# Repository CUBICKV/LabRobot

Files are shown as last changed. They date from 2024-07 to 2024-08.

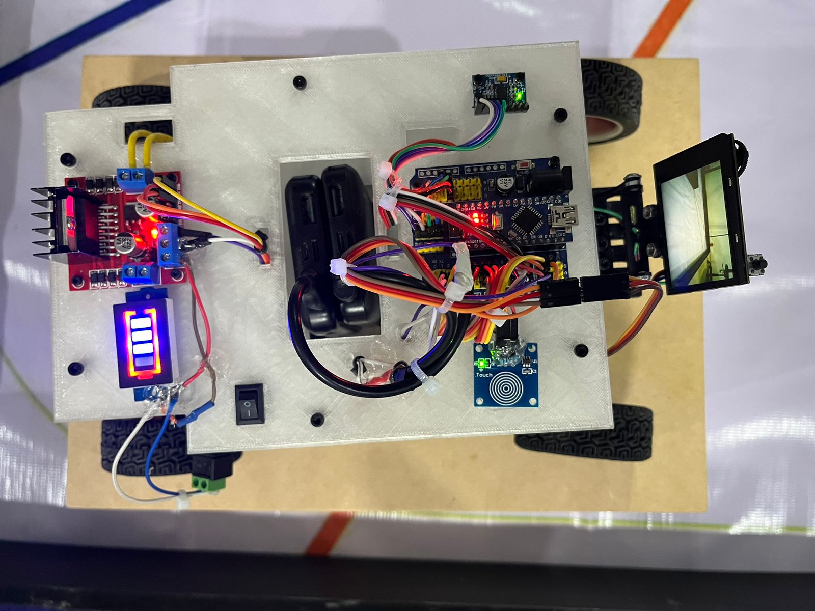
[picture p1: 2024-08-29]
v-photos/SUPERIOR.jpg

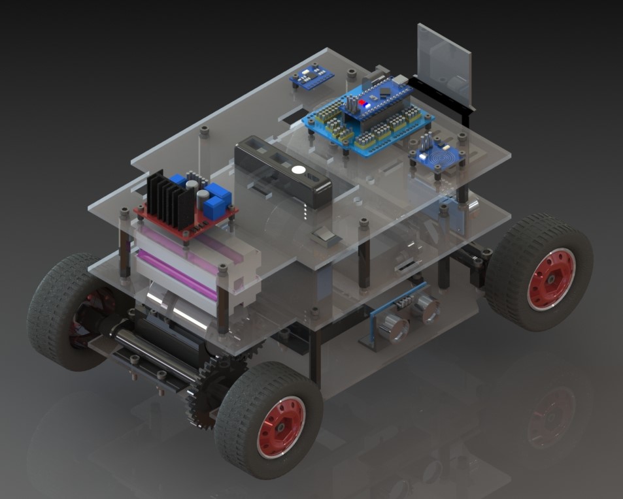
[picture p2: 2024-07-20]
v-photos/ISOMETRICO_4.JPG

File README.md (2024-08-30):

LabRobot
====

El robot nombrado “MATE” es un vehículo autónomo diseñado en un software de CAD, y con circuitos en simuladores electrónicos, programado en la plataforma ARDUINO.
Para el sistema de control, se utilizó una placa de expansión de Arduino nano la cual nos permitió usar sus pines junto a los cables jumpers, para ahorrar nodos de soldadura en el cableado.
Los niveles lógicos a trabajar para el control, se establecieron a 5v, el voltaje de funcionamiento del Arduino nano. Los modulos seleccionados fueron los que tuvieron ese mismo nivel.
Los componentes junto con sus funciones son:
Giroscopio MPU6050: Es un módulo que me permite saber la orientación y ángulo de giro en el Eje Z, para poder conocer mi sentido de giro y mi localización angular en el plano.
Sensor Touch de inducción: Es un sensor táctil, que realiza la misma función de un botón, pero le da una mayor estética al encendido, y nos ahorra el cableado del botón, al igual que es más grande que un botón convencional y menos estorboso
Micro Switch: Nos envía la energía de la Power bank para poder alimentar el sistema de control electrónico.
Puente H: Este es la interfaz de potencia que tiene el cerebro con el motor DC para la tracción trasera del vehículo.
Husky Lens: Es la cámara de visión artificial, conectada con un protocolo de comunicación al cerebro, procesa los datos de los objetos y los envía al control.
Sensor ultrasónico: Se colocaron 3 sensores ultrasónicos en la parte frontal, y en los dos laterales delanteros, para poder crear una referencia de donde se encuentran las paredes.
Arduino nano: Es el cerebro principal, se ocupan todos los pines digitales para poder controlar y recibir los datos de los sensores y componentes electrónicos. Tambien se conecta la cámara. Los protocolos utilizados son los siguientes:
-I2C: Para la cámara de visión artificial.
-PWM: Se ocupa para controlar el servo-motor y el puente h.
-Pulsos: Los recibe y envía para el puente h, el sensor capacitivo y los sensores ultrasónicos.
Indicador de batería: Se coloco un indicador de batería para conocer el voltaje actual de las celdas de litio.
Para la gestión de energía, es regla indispensable siempre conseguir una fuente para potencia y una independiente para control; tambien es preciso no combinar voltajes entre sí, es por eso que, para ahorrar un circuito de regulación, colocamos una tercera fuente de voltaje para el servo-motor.
Esta separación previene el ruido eléctrico y los sobre picos de voltaje que se puedan generar y alteren el procesador del Arduino.
Las fuentes se compraron calculando el consumo que podría tener cada sistema por separado, los cálculos estan registrados en la bitacora, y los resultados son estos:
Control:
-Arduino nano: 64mA
-MPU-6050: 45mA
-Sensor inductivo: 5mA
-Puente H: 36mA
-Husky Lens: 230mA
-3 Sensores Ultrasónicos: (40mA)3x 
Se estableció una Power bank exclusivamente para este sistema, de esa forma queda aislado de cualquier rebote, y nos brinda la energía suficiente para no tener fallas de corriente.
Servo-motor:
-Servo-motor: 1A
La fuente se estableció como una Power bank de 5v, en este caso, obtenemos una fuente que alimenta a un solo componente fuerte y evita el ruido
Motor DC:
-Motor 0.6A
-Indicador batería 0.1A
La fuente se estableció a base de 4 celdas 18650 en serie, para sumar voltajes, de esa forma obtenemos una potencia mayor a la de nuestra carga. 
Despues del cálculo de las fuentes, conseguimos los cargadores necesarios para poder recargas nuestras baterías y obtuvimos un cálculo con el consumo y la carga, que nos indicó un maximo de 4 horas de autonomía con lapsos de 2.6 horas de carga entre cada lapso.
Todas las fuentes se encuentran con un indicador de carga para saber en qué momento requieren ser recargadas; las Power bank se encuentran unidas por la tierra, para poder controlar el servo, pero las cedas de litio se encuentran aisladas y solo se permite el paso de corriente al motor a través del puente H.
Una vez conociendo la distribución de los elementos y los modulos electrónicos, el diseño final lo logramos pasando a digital todos los componentes, utilizando herramientas como vernier y Micrometro, para tener una precisión en las piezas.
En el software Solid Works recreamos los elementos y empezamos el diseño de los mecanismos y la estructura. Se diseño con 3 pisos para poder tener un control y ruteado de cables lo más estético y eficiente posible.
El primer piso se establecido solo para las partes mecánicas de dirección y tracción, al igual que los sensores ultrasónicos para poder crear un sistema de radar de posición de las paredes.
Se coloco el soporte para el motor, servo-motor y la base para las baterías Power bank. Y 4 soportes para mantener el piso 2.
En el segundo piso, se colocó en la parte delantera el soporte para la cámara, el hueco para las Power bank y en la parte trasera, las celdas de litio, junto con el conector de las baterías; igualmente se colocó 6 pilares para sostener el tercer piso.
Con el fin de que este lo más aislado del ruido que pueda generar los motores, se colocó la electronica en el tercer piso, teniendo el módulo de potencia (puente H, indicador de baterías y switch) en la parte trasera, el hueco de las Power bank en el centro, y en la parte frontal, el Arduino con el shield de expansión, el sensor Touch y el módulo MPU-6050.
Todo el sistema mecánico y electrónico y la estructura, estan fijos en su mayoría con tornillería de Acero al Carbon, y en algunas partes con silicón, el cableado soldado está cubierto con cinta doble cara y todo esta ruteado alrededor de los huecos y soportes que se dejaron en la estructura con cintos.
La estructura fue impresa en su totalidad en colores blanco y negro, dejando las BASES en blanco y los soportes y mecanismos color negro para dar contraste. El material utilizado fue el PET, ya que la impresora con que contamos es de materiales limitados y el más fuerte y resistente era el PET, por lo que nuestras piezas cuentan con una densidad del 40%, dándonos el nivel necesario entre peso y dureza.
La normativa indicaba que debían ser visibles todos los componentes, mecanismos y cableados, por eso se eligió un diseño estructural sencillo de varios pisos. Las dimensiones del auto fueron medidas en el Software Solid Works para cumplir con las normas de dimensiones y maso del vehículo, quedando como:
Medida X: 285mm
Medida Y: 195 mm
Medida Z: 200 mm
Peso: 1378g
El modelo resultante consta de cuatro ruedas de tipo neumático con un perímetro de 10cm, de las cuales dos son traseras, y se encuentran unidas por una varilla de transmisión, esta varilla se mueve en conjunto con las ruedas, gracias a un par de engranajes, de 30 y 17 dientes para la varilla y el engranaje del motor, respectivamente, el engranaje del motor fue impreso y moldeado a la forma de eje del motor con una pistola de calor. 
Nuestro motor es un motorreductor modelo TS-37GB330 de la marca AZSSMUK, sus especificaciones técnicas son las siguientes: 
Voltaje nominal: 12v
Revoluciones por minuto: 45-5400 rpm
Radio del eje: 37mm
Torque: 0.5kg/cm
Reducción: 1/9
Despues de considerar diferentes modelos, que fueron desde uno para Go-Car o uno de bomba de diafragma, se decidió cambiar fuerza por velocidad para poder mover el auto con un bajo consumo energético.
El motor está controlado por un módulo de puente H “L298n”, el cual nos permite controlar el sentido de giro y la velocidad, se conectó en el lateral derecho, precisamente para que el cableado estuviera lo más cercano entre el puente, la batería y el motor. Igualmente, si manteníamos el peso cercano al motor, reduciríamos la necesidad de potencia para poder romper el momento de inercia del vehículo.
La dirección del vehículo está colocada en la parte frontal con un servo-motor de 15kg, (entre mayor sea la capacidad del motor, menos energía requiere por un mayor esfuerzo), este está unido a un engranaje de 22 dientes que hace la función de un piñón, por medio de tornillos, de forma que cuando el servo gira entre 0° y 180°, el piñón en conjunto con una cremallera, convierten el movimiento circular en lineal. Con una relación de 1mm por cada 5° de giro.
Los ejes de las llantas son independientes, y estan sobre un eje rotativo sujeto a la placa de soporte “BASE_1” este se encarga de girar el eje de las llantas, y sostener el vehículo sobre su tapa.
Los ejes rotativos se encuentran unidos en 3 zonas por ejes, para darle movimientos consistentes e iguales a las 2 llantas, se encuentra uno en la parte inferior para mantener nivelados ambos ejes; en la parte superior a la altura del eje, para darles un movimiento proporcional y estabilidad entre sí; y finalmente, se encuentra la cremallera del motor en la parte trasera del eje, para transmitir el movimiento del servo-motor.
El servo motor se encuentra con una inclinación para aplicar presión del piñón sobre la cremallera, de esa forma, evitamos que se corra la barra por soltura, y concentramos la fuerza correctamente para la transmisión circular-lineal.
La distribución de la dirección se encuentra en la parte frontal, para tener una estabilidad y mejor control de la dirección, asi como una compensación para el peso de baterías y componentes electrónicos en el control.
Como todo buen proyecto, se debieron hacer cálculos cinemáticos para evaluar las velocidades del vehículo, estan registradas en la bitacora, y como resultado nos dio:
Velocidad lineal de 3km/h.
Una vez probado el vehículo y haciendo estimaciones que tenemos en la bitacora, se obtuvo que, al aplicar la velocidad estimada al peso del vehículo, junto al sistema reductor de engranajes en la transmisión, obtuvimos un resultado un tanto esperado:
El vehículo se desplaza de 0.667 a 0.706 km/h, con mayor tiempo, esto puede indicar que existe una aceleración que incrementa con el tiempo, al romper el momento de inercia de la masa del vehículo, le resulta más facil al motor moverse y eso implica que su velocidad crucero debe estar entre los 10 o 15 segundos, sin embargo, al tener que dar constantemente vueltas, podemos decir que su velocidad estándar estará entre 0.65 y 0.7 km/h.
El torque del vehículo depende de los componentes electromecánicos, en este caso de los mecanismos de tracción y dirección.
Para tracción, podemos iniciar con el torque del motor que este sujeto a un mecanismo de engranajes que cambia distancia por fuerza, es decir que aumenta nuestro torque en una relación de 0.55 a 1, es decir que incrementa en un 55% la fuerza de torque del motor, dando un resultado de: 9kg/cm^2
En cuanto a la dirección delantera, el mecanismo piñón cremallera, tiene una conversión circular a lineal con la relación es 5:1, pero en cuanto a fuerza, esto se mantiene igual, es decir una relación 1:1 en cuanto a torque, por lo que la fuerza de giro es igual a la del reductor de servo, es decir, una relación de 15Kg/cm^2. Esto solo es dinámico, pero la realidad es que los esfuerzos dependen de la resistencia de las piezas y sus propiedades (Tabla en la bitacora).
Todos los componentes estan calculados con su maximo esfuerzo energético, y su maximo peso, al igual que su minimo rendimiento de fuerza o velocidad, esto para poder tener una tolerancia de funcionamiento ante eventualidades.
El codigo está seccionado para una mejor interpretación, en la primera parte, estan incluidas las librerias, las cuales controlan la cámara, el monitor serial, el protocolo I2C, el giroscopio, y el servomotor.
Despues declaramos los pines del Arduino, desde el 3 hasta el 12, y creamos los objetos que serán controlados tanto para el protocolo I2C como el servo motor para PWM.
Declaramos las variables de control para el puente H.
Declaramos las variables de control para el giroscopio.
Declaramos los ángulos para el servo en cada posición.
Declaramos las variables para los 3 ultrasónicos.
Declaramos las condiciones para el sensor táctil.
Ponemos variables y colores para la cámara.
Definimos valores para la dirección.
Iniciamos el “Void setup”, en el cual inicializamos la comunicación serial a una velocidad de 115200, y tambien el protocolo Wire, para el mpu y su dirección, damos un mensaje de inicialización para confirmar que se inició todo, y entramos a un ciclo para iniciar la cámara, cuando este termine, definimos la función de los pines, e iniciamos todo para que comience apagado y en posición recta. Esperamos 2 segundos por algun fallo y da un mensaje de “LISTO” para comprobar que todo este correcto.
Iniciamos el “Void Loop”, Iniciamos la condición de inicio en la parte de arranque con el sensor Touch, este es un siclo anidado en donde se detecta el nivel del botón y en cuanto a eso, nos indica para pasar al siguiente bloque que sería el del sentido.
En este bloque, el robot está programado para avanzar recto hasta detectas 1 metro de distancia frente a él, en ese punto, va a detenerse, medir distancias y determinar si está en sentido de las manecillas del reloj o en sentido contrario. Una vez que determine eso, lo guardara en una variable (PARED) y esta determinara las direcciones de giro posteriores. El robot girara en el sentido indicado y comenzara el siclo de sensores.
En el ciclo de sensores, está el bloque de verificación, donde se muestran en el monitor serial todos los datos de los sensores y la cámara, así como los necesarios para el control del robot y detección de objetos.
Pasamos al bloque de giroscopio, donde se realiza una lectura del sensor, y usamos el ángulo Z para definir la orientación del vehículo, en este caso entra a condicionales que determinaran la zona donde se encuentra y el ángulo que lleva en ese momento, así como un conteo de la vuelta en donde se encuentra.
Pasando al bloque de Ultrasónico, tenemos el control de los 3 ultrasónicos, cada uno despues del otro, con 1 milisegundo de diferencia, usando la formación de escritura para centímetros.
Despues de eso, pasamos al apartado de la HUSKYLENS, donde verificamos que el protocolo sea correcto y que se encuentren objetos en pantalla, si todo eso es correcto, entonces llamaremos a la función HUSKYLENSResult, que se encuentra despues de concluir el Void Loop.
La función HUSKYLENSResult, detecta el bloque donde se encuentra el color, y al clasificarlo con un switch y ciclos if, nos guarda las cordenadas del bloque VERDE y el bloque ROJO, por medio del ID de la cámara (Para guardar los objetos en la cámara, es necesario seguir las instrucciones de la página de la Husky Lens para objetos múltiples).
Siguiendo a la Zona de control donde se procesarán todos los datos de los sensores, se coloca una secuencia de inicio, para poder detectar el sentido de giro del vehículo, usando los 3 sensores ultrasónicos, acto seguido, se guardan los datos y se ingresa al ciclo de control.
Este consta de un PID, el cual se encargará de verificar la dirección y sentido en corrección del servo-motor, dándonos una dirección y un tiempo de giro, para poder estabilizar la posición en las vueltas. Este es a base de los ángulos del giroscopio, para brindar estabilidad.
Tambien tenemos una secuencia para las esquinas, la cual detecta cuando una pared se acerca y coloca la secuencia de giro, dependiendo el sentido de giro que tenemos, a su vez, en detección automática de la tercera vuelta, se detiene en su zona de inicio, para poder dar fin a su recorrido.
El PID está basado en 4 partes, o 4 PID dependientes, estos serían:
Vuelta en sentido horario:
1.- El PID de distancias, mantiene a distancias iguales de las paredes el vehículo.
2.- El PID del ángulo, mantiene en una línea perpendicular a las paredes al vehículo.
Vuelta en sentido antihorario:
1.- El PID de distancias, mantiene a distancias iguales de las paredes el vehículo.
2.- El PID del ángulo, mantiene en una línea perpendicular a las paredes al vehículo.
Estos se encargan de enviar instrucciones con los valores al motor servo para girar y mantenerse recto hasta las secuencias de esquinas, al igual que el contador que se encuentra para detener el vehículo en la 4ta vuelta al inicio. El vehículo se controlo en su velocidad crucero del 80% de potencia y un 50% para las vueltas, por estabilidad.

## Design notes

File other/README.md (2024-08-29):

OTHER
====

Arduino configurations to load the program.

Arduino IDE 2.3.2

El vehiculo debe encenderce en la posición de inicio, se enciende el interruptor, y se espera a que las llantas delanteras se acomoden, acto seguido, se acomodan manualmente para que esten paralelas a las traseras. 
Para iniciar el movimiento, se debe de presionar el sensor táctil y retirarse de la pista.

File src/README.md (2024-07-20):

Control software
====

-PROGRAM ONE IS INCLUDED, WHERE WE PLACE A DIRECTION AND LINEAR ADVANCE CONTROL, AS WELL AS THE CONNECTION AND TESTING OF ALL THE SENSORS.

-THE PROGRAM IS COMPILED AND READ WITH ARDUINO, WHICH IS DOWNLOADED FROM THE OFFICIAL ARDUINO SITE.

LINK:https://www.arduino.cc/en/software

-I INCLUDE THE .ZIP LIBRARIES TO COMPILE THE PROJECT.

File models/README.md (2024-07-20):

MODELS
====

Archivos .STL para configurar las piezas en cualquier tipo de impresora.

Archivos .Gcode listos para imprimir en una Ender 3.

Configuraciones:

-PET 40%

-Sin balsa

-Soportes 

-Concéntricos

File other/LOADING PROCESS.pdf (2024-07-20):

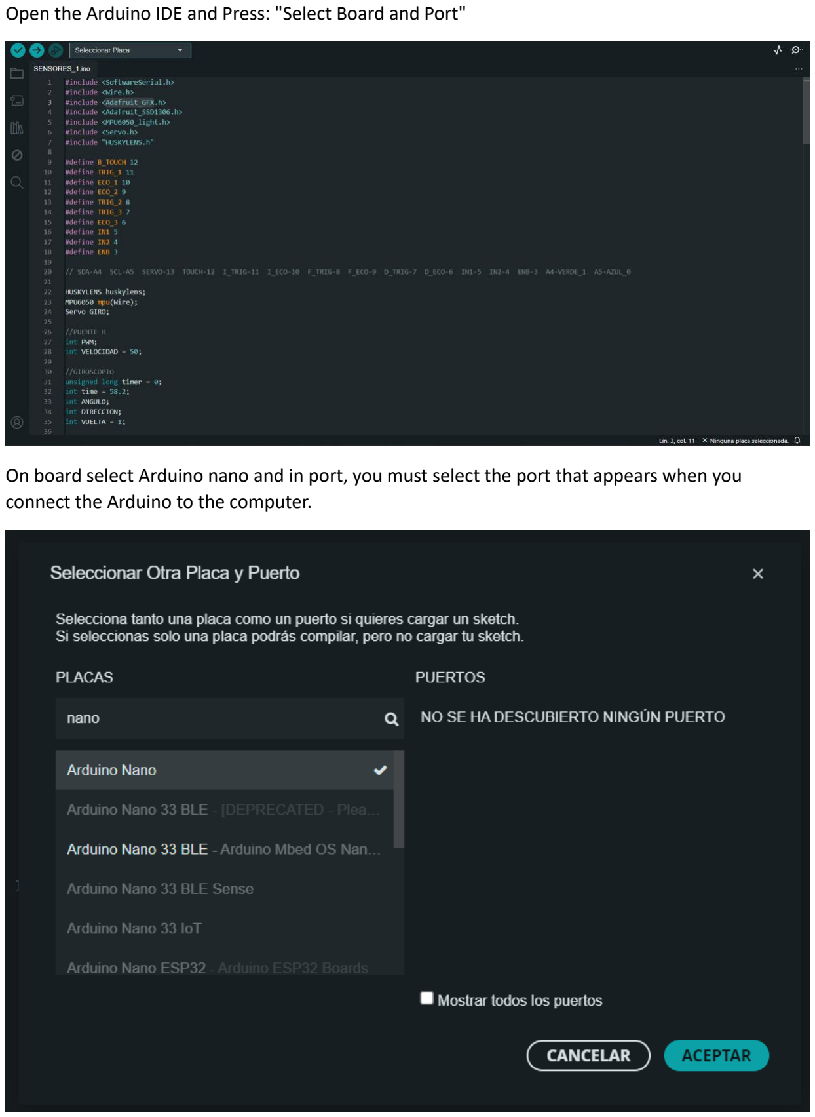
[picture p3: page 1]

Open the Arduino IDE and Press: "Select Board and Port"

On board select Arduino nano and in port, you must select the port that appears when you connect the Arduino to the computer.

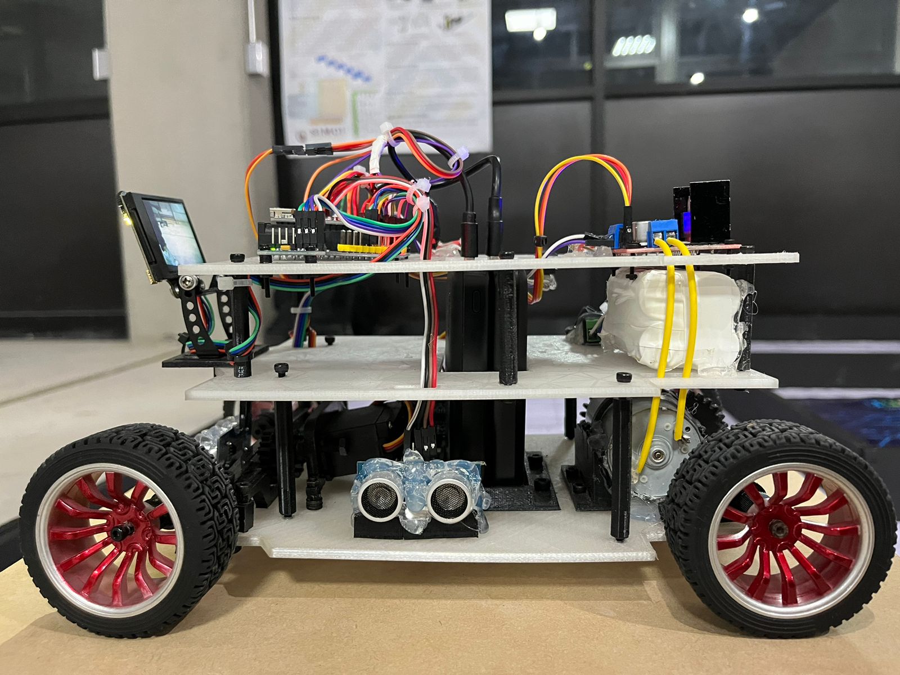
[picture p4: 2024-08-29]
v-photos/IZQUIERDA.jpg

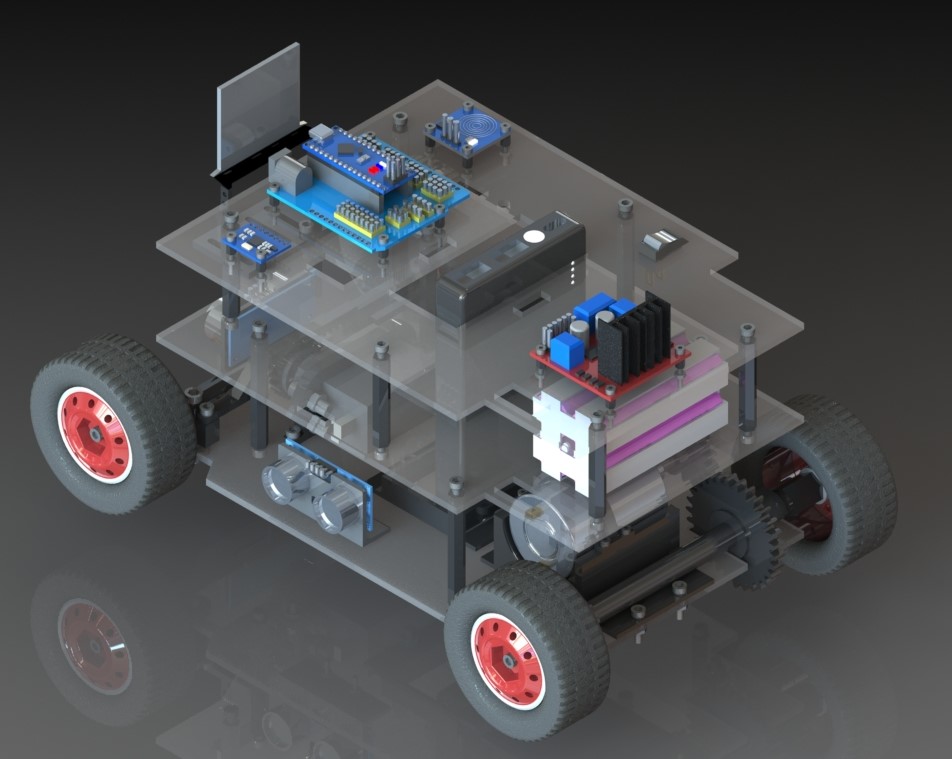
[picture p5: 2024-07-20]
v-photos/ISOMETRICO_3.JPG

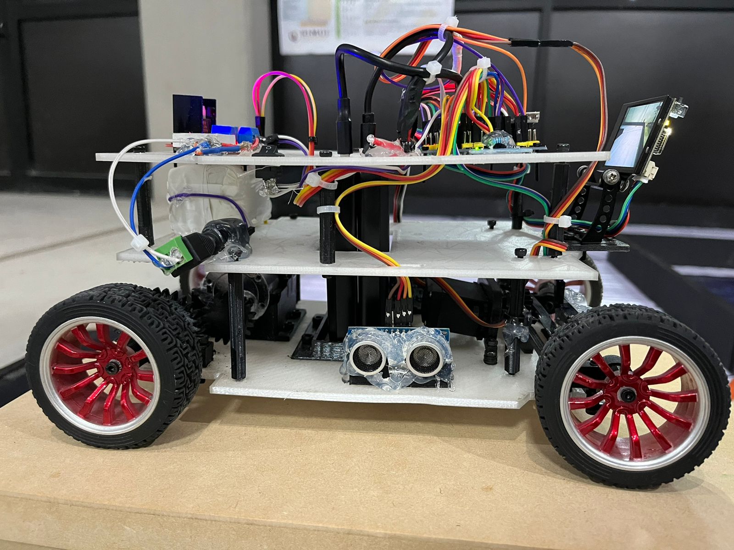
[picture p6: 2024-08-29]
v-photos/DERECHA.jpg

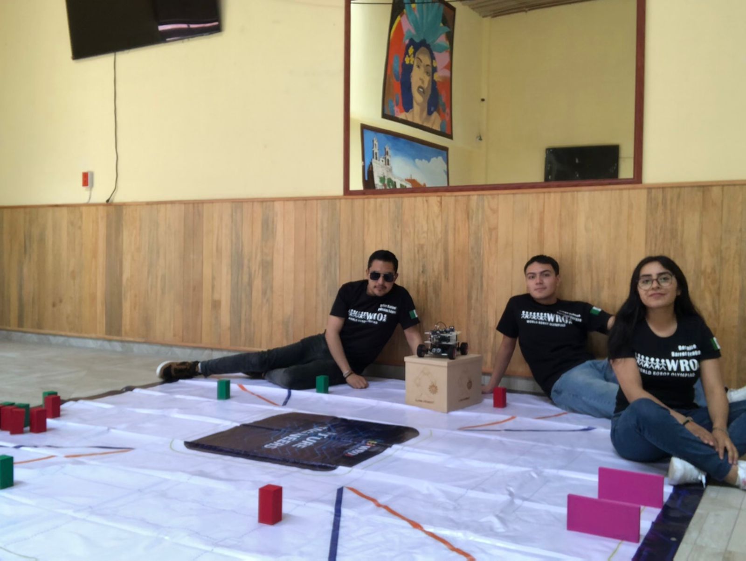
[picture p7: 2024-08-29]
t-photos/DIVERTIDA.jpg

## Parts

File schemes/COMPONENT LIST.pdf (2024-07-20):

LAB ROBOT WRO MANUFACTURA.

MATERIAL | IMAGEN | CANTIDAD

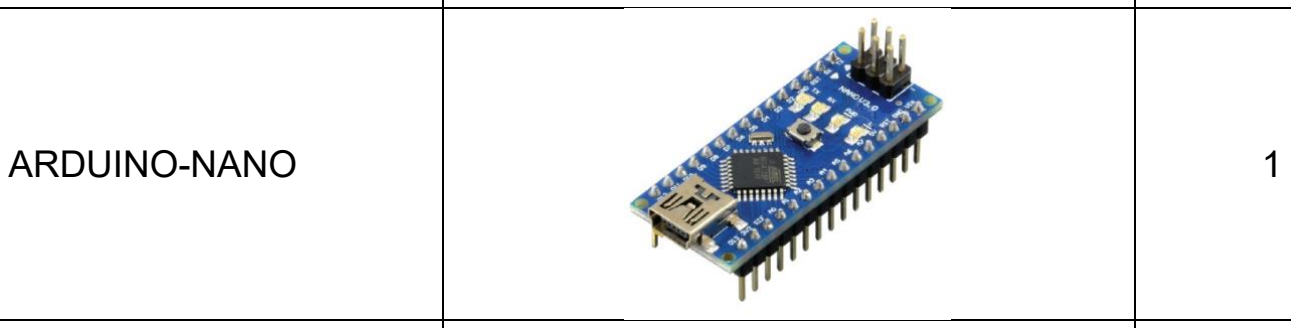
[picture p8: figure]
ARDUINO-NANO

BARILLA TRANSMISIÓN_1 | | 1

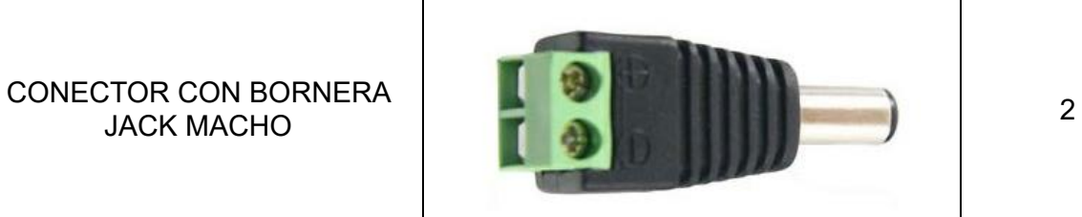
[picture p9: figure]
CONECTOR CON BORNERA JACK MACHO

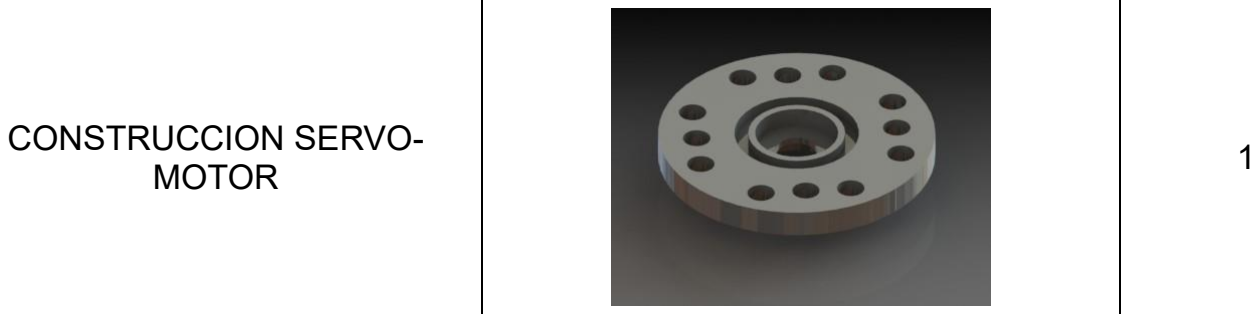
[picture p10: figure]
CONSTRUCCION SERVO-MOTOR
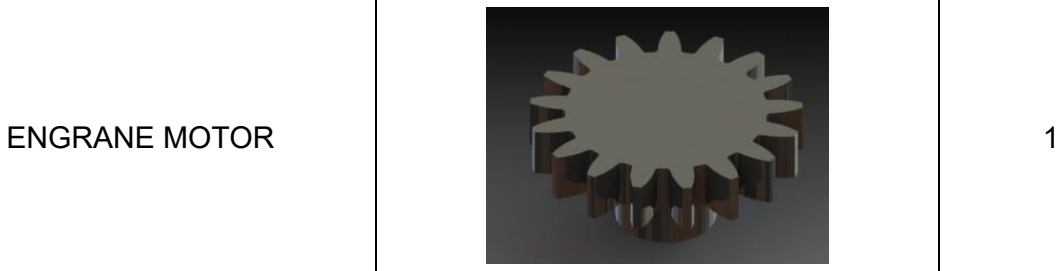
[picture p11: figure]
ENGRANE MOTOR
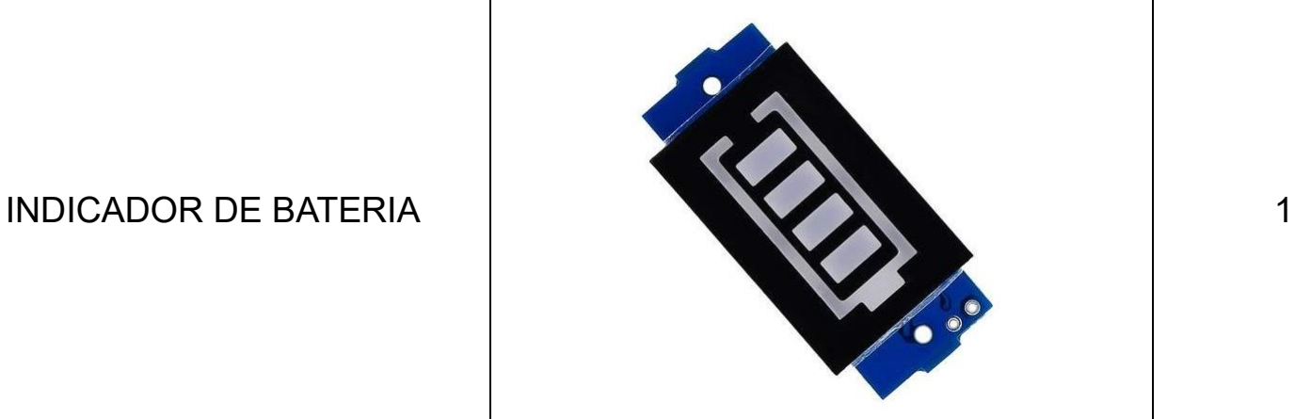
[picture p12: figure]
INDICADOR DE BATERIA

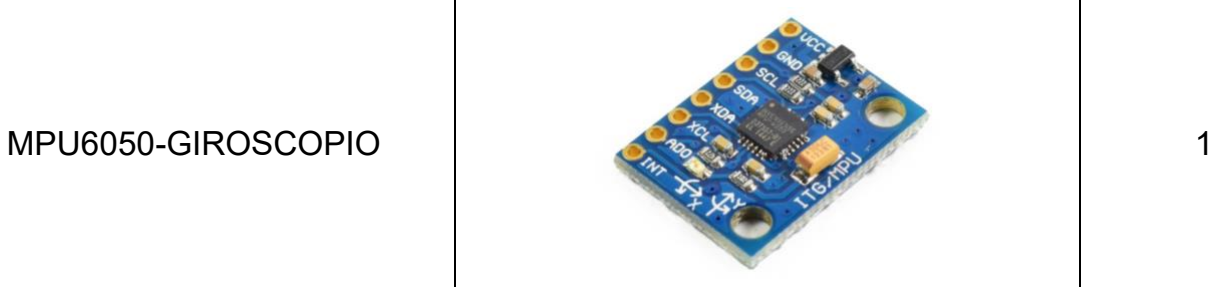
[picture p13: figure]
MPU6050-GIROSCOPIO
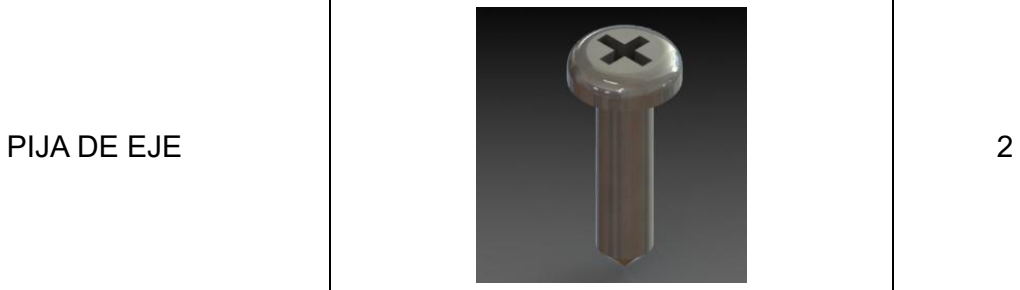
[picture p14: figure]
PIJA DE EJE
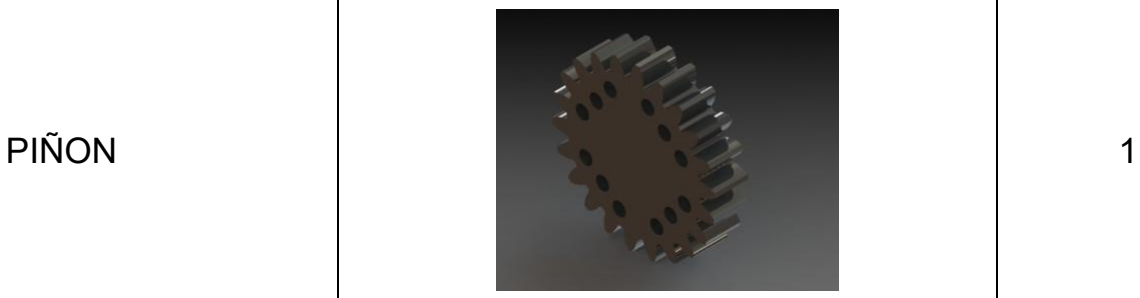
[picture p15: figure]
PIÑON

PISO_2
PORTA VARILLA LLANTA DELANTERA
POWER BANK 5V 5A

SENSOR-TACTIL
SEPARADOR TARJETAS

SEPARADOR_2
SERVO-MOTOR
SOPORTE BATERIAS_1

SOPORTE MOTOR_1
SOPORTE MOTOR_2
SOPORTE SERVO-MOTOR

SWITCH
TORNILLO M2-08; KID TORNILLERIA; TORNILLO M2-12; TORNILLO M2-16; TORNILLO M3-08; TORNILLO M3-12; TORNILLO M4-08; TORNILLO M4-12; TORNILLO M4-16

TORNILLO M4-20

TORNILLO SERVO-MOTOR

TUERCA M2

KID

VARILLA LLANTA DELANTERA
VARILLA_LLANTA_2

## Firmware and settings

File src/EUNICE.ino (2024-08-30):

//LIBRERIAS
  #include <SoftwareSerial.h>
  #include <Wire.h>
  #include <Adafruit_GFX.h>
  #include <Adafruit_SSD1306.h>
  #include <MPU6050_light.h>
  #include <Servo.h>
  #include "HUSKYLENS.h" 
  #include "I2Cdev.h"

//PINES
  #define B_TOUCH 12
  #define TRIG_1 11
  #define ECO_1 10
  #define ECO_2 9
  #define TRIG_2 8
  #define TRIG_3 7
  #define ECO_3 6
  #define IN1 5
  #define IN2 4
  #define ENB 3
  // SDA-A4  SCL-A5  SERVO-13  TOUCH-12  I_TRIG-11  I_ECO-10  F_TRIG-8  F_ECO-9  D_TRIG-7  D_ECO-6  IN1-5  IN2-4  ENB-3  A4-VERDE_1  A5-AZUL_0  

//OBJETOS
  HUSKYLENS huskylens;
  MPU6050 mpu(Wire);
  Servo GIRO;

//PUENTE H
  int PWM = 0;
  int VELOCIDAD = 0;

//GIROSCOPIO
  unsigned long timer = 0;
  int INICIAL;
  int CONTINUO;
  float ANGULO;
  int ZONA = 0;
  int VUELTA = 1;

//SERVO
  int L_DERECHA = 170;
  int L_IZQUIERDA = 50;
  int L_CENTRO_I = 160;
  int L_CENTRO_D = 60;
  int L_CENTRO = 100;

//ULTRASONICOS
  int DURACION_1 = 0;
  int DURACION_2 = 0;
  int DURACION_3 = 0;
  int DIST_FRENTE = 0;
  int DIST_IZQUIERDA = 0;
  int DIST_DERECHA = 0;
  int time = 58.2;

//TACTIL
  int TACTIL;
  int ESTADO_BOTON = 0;
  int ACTIVO = 0;

//CAMARA
  int X = 0;
  int VERDE;
  int Y = 0;
  int ROJO = 0;
  int X_CENTRO = 160;
  int Y_CENTRO = 120;

//DIRECCIÓN
  int IZQUIERDA = 0;
  int DERECHA = 0;
  int PARED = 0;
  int EXTRA = 0;

//PID
  int ET; 
  int SD;
  int SM;
  int dE;
  int Ep;
  int iE;
  int Eip;
  int Ei;
  int PID;
  float t;
  int ET_2; 
  int SD_2;
  int SM_2;
  int dE_2;
  int Ep_2;
  int iE_2;
  int Eip_2;
  int Ei_2;
  int PID_2;
  float t_2;
  int KP = 1;
  float KI = 0.1;
  float KD = 0.1;


void setup() {
  Serial.begin(115200);
  Wire.begin();
  mpu.begin();    
  byte status = mpu.begin();    
  Serial.println(status);
  while(status!=0){ }
  mpu.calcGyroOffsets();
  Serial.println("INICIO");
  while(status!=0){ };

  while (!huskylens.begin(Wire)){
    Serial.println(F("¡COMUNICACIÓN FALLIDA!"));
    Serial.println(F("1.POR FAVOR REVISE EL PROTOCOLO \"Protocol Type\" in HUSKYLENS (General Settings>>Protocol Type>>I2C)"));
    Serial.println(F("2.POR FAVOR REVISE LA CONEXIÓN.")); 
    delay(100);
  }

  pinMode(TRIG_1,OUTPUT);
  pinMode(ECO_1, INPUT);
  pinMode(TRIG_2,OUTPUT);
  pinMode(ECO_2, INPUT);
  pinMode(TRIG_3,OUTPUT);
  pinMode(ECO_3, INPUT);
  pinMode(IN1, OUTPUT);
  pinMode(IN2, OUTPUT);
  pinMode(B_TOUCH, INPUT);
  GIRO.attach(13);

  digitalWrite(IN1, LOW);
  digitalWrite(IN2, HIGH);
  analogWrite(ENB, 0);
  delay(2000);
  GIRO.write(L_CENTRO);
  delay(2000);
  Serial.println("LISTO");
 }


void loop() {
  //**************************************INICIO**************************************
    //ARRANQUE
      TACTIL = digitalRead(B_TOUCH);
      if(TACTIL == HIGH){
        delay(20);
        TACTIL = digitalRead(B_TOUCH);
        if(TACTIL == LOW && ESTADO_BOTON == 1){
          ESTADO_BOTON = 0;
          Serial.println("ESTADO = 0");
          delay(1000);
        }
        if(TACTIL == LOW && ESTADO_BOTON == 0){
          ESTADO_BOTON = 1;
          Serial.println("ESTADO = 1");
          delay(1000);
        }
      }

    //SENTIDO
      if(ESTADO_BOTON == 1){
        if(PARED == 0 && ACTIVO == 0){
          if(DIST_FRENTE > 101 || DIST_FRENTE == 0){
            VELOCIDAD = 50; PWM = map(VELOCIDAD, 0, 100, 0, 250); analogWrite(ENB, PWM);
          } 
          digitalWrite(TRIG_2, HIGH);     
          delay(1);        
          digitalWrite(TRIG_2, LOW);
          DURACION_2 = pulseIn(ECO_2, HIGH);     
          DIST_FRENTE = DURACION_2 / time;
          Serial.println(DIST_FRENTE);
          delay(10);
          if(DIST_FRENTE <= 100 && DIST_FRENTE > 0){
            VELOCIDAD = 0; PWM = map(VELOCIDAD, 0, 100, 0, 250); analogWrite(ENB, PWM); ACTIVO = 1;
          }
        }
        if(ACTIVO == 1){
          digitalWrite(TRIG_1, HIGH); 
          delay(1);
          digitalWrite(TRIG_1, LOW);
          DURACION_1 = pulseIn(ECO_1, HIGH);
          DIST_IZQUIERDA = DURACION_1 / time; 
          digitalWrite(TRIG_3, HIGH);     
          delay(1);        
          digitalWrite(TRIG_3, LOW);
          DURACION_3 = pulseIn(ECO_3, HIGH);     
          DIST_DERECHA = DURACION_3 / time;
          if(DIST_DERECHA > 0 && DIST_IZQUIERDA > 0){
            if(DIST_DERECHA > DIST_IZQUIERDA){
              PARED = 1; IZQUIERDA = 0; DERECHA = 1;//GIRO A LA DERECHA
            }
            if(DIST_IZQUIERDA > DIST_DERECHA){
              PARED = 2; IZQUIERDA = 1; DERECHA = 0;//GIRO A LA IZQUIERDA
            }
            if(PARED == 1 && DERECHA == 1){
              GIRO.write(L_DERECHA); delay(500); EXTRA = 0;
            }
            if(PARED == 2 && IZQUIERDA == 1){
              GIRO.write(L_IZQUIERDA); delay(500); EXTRA = 200;
            }
            VELOCIDAD = 50; PWM = map(VELOCIDAD, 0, 100, 0, 250); analogWrite(ENB, PWM);
            delay(1300 + EXTRA);
            if(DERECHA == 1){
              GIRO.write(L_IZQUIERDA); delay(100); GIRO.write(L_CENTRO_D); delay(100); ACTIVO = 2;
            }
            if(IZQUIERDA == 1){
              GIRO.write(L_DERECHA); delay(100); GIRO.write(L_CENTRO_I); delay(100); ACTIVO = 2;
            }
            VELOCIDAD = 80; PWM = map(VELOCIDAD, 0, 100, 0, 250); analogWrite(ENB, PWM);
          }
        }
      }
  //**************************************SENSORES**************************************
    if(ACTIVO == 2){
      //VERIFICACIÓN
        Serial.print("DISTANCIA IZQUIERDA: "); Serial.print(DIST_IZQUIERDA); Serial.println("cm");
        Serial.print("DISTANCIA DERECHA: "); Serial.print(DIST_DERECHA); Serial.println("cm");
        Serial.print("DISTANCIA FRENTE: "); Serial.print(DIST_FRENTE); Serial.println("cm");
        Serial.print("ANGULO: "); Serial.print(ANGULO); Serial.println("°");
        Serial.print("ZONA: "); Serial.print(ZONA);
        Serial.print("VUELTA: "); Serial.print(VUELTA); Serial.println(" de 3");
        Serial.print("VELOCIDAD: "); Serial.print(VELOCIDAD); Serial.println("%");
        Serial.println(String()+F("VERDE X = ")+X+F(" ")+VERDE);
        Serial.println(String()+F("ROJO X = ")+X+F(" ")+ROJO);

      //GIROSCOPIO
        if(INICIAL == 0){
          mpu.update();  
          if((millis()-timer)>100){
            INICIAL = (mpu.getAngleZ());
            timer = millis(); 
          }
        }
        mpu.update();  
        if((millis()-timer)>10){  
          CONTINUO = (mpu.getAngleZ());
          timer = millis(); 
          delay(50);
          ANGULO = (CONTINUO - INICIAL);
          if(PARED == 2){ //IZQUIERDA
            ANGULO = ANGULO;
          } 
          if(PARED == 1){ //DERECHA
            ANGULO = (-1*(ANGULO));
          }                                       
          if(ANGULO <= 90 && ANGULO >=1){
            ZONA = 1;
          }

          if(ANGULO <= 180 && ANGULO >= 91){
            ZONA = 2;
          }

          if(ANGULO <= 270 && ANGULO >= 181){
            ZONA = 3;
          }

          if(ANGULO <= 360 && ANGULO >= 271){
            ZONA = 4;
          }
          if(ANGULO <= 450 && ANGULO >=361){
            ZONA = 5;
          }

          if(ANGULO <= 540 && ANGULO >= 451){
            ZONA = 6;
          }

          if(ANGULO <= 630 && ANGULO >= 541){
            ZONA = 7;
          }

          if(ANGULO <= 720 && ANGULO >= 631){
            ZONA = 8;
            VUELTA = 2;
          }
          if(ANGULO <= 810 && ANGULO >= 721){
            ZONA = 9;
          }

          if(ANGULO <= 900 && ANGULO >= 811){
            ZONA = 10;
          }

          if(ANGULO <= 990 && ANGULO >= 901){
            ZONA = 11;
          }

          if(ANGULO <= 1080 && ANGULO >= 991){
            ZONA = 12;
            VUELTA = 3;
          }
          if(ANGULO <= 1170 && ANGULO >= 1081){
            ZONA = 13;
            VUELTA = 4;
          }
        }

      //ULTRASONICO
        digitalWrite(TRIG_1, HIGH); 
        delay(1);
        digitalWrite(TRIG_1, LOW);
        DURACION_1 = pulseIn(ECO_1, HIGH);
        DIST_IZQUIERDA = DURACION_1 / time; 
        digitalWrite(TRIG_2, HIGH); 
        delay(1);
        digitalWrite(TRIG_2, LOW); 
        DURACION_2 = pulseIn(ECO_2, HIGH);
        DIST_FRENTE = DURACION_2 / time;
        digitalWrite(TRIG_3, HIGH);     
        delay(1);        
        digitalWrite(TRIG_3, LOW);
        DURACION_3 = pulseIn(ECO_3, HIGH);     
        DIST_DERECHA = DURACION_3 / time;
      //HUSKYLENS
        if (!huskylens.request()){ Serial.println(F("¡Comunicación fallida , revise conexiones fisicas!"));}
        else if(!huskylens.isLearned()){ Serial.println(F("¡No tiene ningun objeto para elegir, elija uno!"));}
        else if(!huskylens.available()){ Serial.println(F("¡No aparecen bloques en la pantalla!")); X = 0; Y = 0; }
        else{
          Serial.println(F("###########")); 
          if (huskylens.available()){
            HUSKYLENSResult result = huskylens.read(); printResult(result);
          }
        }

  //**************************************CONTROL**************************************
      if(ZONA != 13 && VUELTA != 4){
        //PARED 1
          if(PARED == 1){
            //VARIABLES
              SM = (DIST_IZQUIERDA);
              SD = (20);
            //PID
              ET = SD - SM; //ERROR PROPORCIONAL 
              dE = (ET - Ep)/t; //ERROR DIFERENCIAL
              Ep = ET;
              iE = Eip + (t*ET); //ERROR INTEGRAL
              Eip = Ei;
              t = t + (0.053 + (PID/100)); //TIEMPO 
              PID = (KP*ET)+(KI*iE)+(KD*dE); //PID
              if(DIST_IZQUIERDA < 40 || DIST_IZQUIERDA < 0){
                GIRO.write(L_IZQUIERDA);
                delay(PID*10);
              }
                //ULTRASONICO
                  digitalWrite(TRIG_1, HIGH); 
                  delay(1);
                  digitalWrite(TRIG_1, LOW);
                  DURACION_1 = pulseIn(ECO_1, HIGH);
                  DIST_IZQUIERDA = DURACION_1 / time; 
                  digitalWrite(TRIG_2, HIGH); 
                  delay(1);
                  digitalWrite(TRIG_2, LOW); 
                  DURACION_2 = pulseIn(ECO_2, HIGH);
                  DIST_FRENTE = DURACION_2 / time;
                  digitalWrite(TRIG_3, HIGH);     
                  delay(1);        
                  digitalWrite(TRIG_3, LOW);
                  DURACION_3 = pulseIn(ECO_3, HIGH);     
                  DIST_DERECHA = DURACION_3 / time;
              if(DIST_DERECHA < 40  || DIST_DERECHA < 0){
                GIRO.write(L_IZQUIERDA);
                delay(PID*5);
              }
            //VARIABLES
              SM_2 = (ANGULO);
              SD_2 = (90*ZONA);
            //PID
              //GIROSCOPIO
                if(INICIAL == 0){
                  mpu.update();  
                  if((millis()-timer)>100){
                    INICIAL = (mpu.getAngleZ());
                    timer = millis(); 
                  }
                }
                mpu.update();  
                if((millis()-timer)>10){  
                  CONTINUO = (mpu.getAngleZ());
                  timer = millis(); 
                  delay(50);
                  ANGULO = (CONTINUO - INICIAL);
                  if(PARED == 2){ //IZQUIERDA
                    ANGULO = ANGULO;
                  } 
                  if(PARED == 1){ //DERECHA
                    ANGULO = (-1*(ANGULO));
                  }                                       
                  if(ANGULO <= 90 && ANGULO >=1){
                    ZONA = 1;
                  }

                  if(ANGULO <= 180 && ANGULO >= 91){
                    ZONA = 2;
                  }

                  if(ANGULO <= 270 && ANGULO >= 181){
                    ZONA = 3;
                  }

                  if(ANGULO <= 360 && ANGULO >= 271){
                    ZONA = 4;
                  }
                  if(ANGULO <= 450 && ANGULO >=361){
                    ZONA = 5;
                  }

                  if(ANGULO <= 540 && ANGULO >= 451){
                    ZONA = 6;
                  }

                  if(ANGULO <= 630 && ANGULO >= 541){
                    ZONA = 7;
                  }

                  if(ANGULO <= 720 && ANGULO >= 631){
                    ZONA = 8;
                    VUELTA = 2;
                  }
                  if(ANGULO <= 810 && ANGULO >= 721){
                    ZONA = 9;
                  }

                  if(ANGULO <= 900 && ANGULO >= 811){
                    ZONA = 10;
                  }

                  if(ANGULO <= 990 && ANGULO >= 901){
                    ZONA = 11;
                  }

                  if(ANGULO <= 1080 && ANGULO >= 991){
                    ZONA = 12;
                    VUELTA = 3;
                  }
                  if(ANGULO <= 1170 && ANGULO >= 1081){
                    ZONA = 13;
                    VUELTA = 4;
                  }
                }
              
                if(INICIAL == 0){
                  mpu.update();  
                  if((millis()-timer)>100){
                    INICIAL = (mpu.getAngleZ());
                    timer = millis(); 
                  }
                }
                mpu.update();  
                if((millis()-timer)>10){  
                  CONTINUO = (mpu.getAngleZ());
                  timer = millis(); 
                  delay(50);
                  ANGULO = (CONTINUO - INICIAL);
                  if(PARED == 2){ //IZQUIERDA
                    ANGULO = ANGULO;
                  } 
                  if(PARED == 1){ //DERECHA
                    ANGULO = (-1*(ANGULO));
                  }                                       
                  if(ANGULO <= 90 && ANGULO >=1){
                    ZONA = 1;
                  }

                  if(ANGULO <= 180 && ANGULO >= 91){
                    ZONA = 2;
                  }

                  if(ANGULO <= 270 && ANGULO >= 181){
                    ZONA = 3;
                  }

                  if(ANGULO <= 360 && ANGULO >= 271){
                    ZONA = 4;
                  }
                  if(ANGULO <= 450 && ANGULO >=361){
                    ZONA = 5;
                  }

                  if(ANGULO <= 540 && ANGULO >= 451){
                    ZONA = 6;
                  }

                  if(ANGULO <= 630 && ANGULO >= 541){
                    ZONA = 7;
                  }

                  if(ANGULO <= 720 && ANGULO >= 631){
                    ZONA = 8;
                    VUELTA = 2;
                  }
                  if(ANGULO <= 810 && ANGULO >= 721){
                    ZONA = 9;
                  }

                  if(ANGULO <= 900 && ANGULO >= 811){
                    ZONA = 10;
                  }

                  if(ANGULO <= 990 && ANGULO >= 901){
                    ZONA = 11;
                  }

                  if(ANGULO <= 1080 && ANGULO >= 991){
                    ZONA = 12;
                    VUELTA = 3;
                  }
                  if(ANGULO <= 1170 && ANGULO >= 1081){
                    ZONA = 13;
                    VUELTA = 4;
                  }
                }
              ET_2 = SD_2 - SM_2; //ERROR PROPORCIONAL 
              dE_2 = (ET_2 - Ep_2)/t_2; //ERROR DIFERENCIAL
              Ep_2 = ET_2;
              iE_2 = Eip_2 + (t_2*ET_2); //ERROR INTEGRAL
              Eip_2 = Ei_2;
              t_2 = t_2 + (0.053 + (PID_2/100)); //TIEMPO 
              PID_2 = (KP*ET_2)+(KI*iE_2)+(KD*dE_2); //PID
              if(PID > 0){
                GIRO.write(L_IZQUIERDA);
                delay(PID*10);
              }
              if(PID < 0){
                GIRO.write(L_IZQUIERDA);
                delay(PID*5);
              }
                //ULTRASONICO
                  digitalWrite(TRIG_1, HIGH); 
                  delay(1);
                  digitalWrite(TRIG_1, LOW);
                  DURACION_1 = pulseIn(ECO_1, HIGH);
                  DIST_IZQUIERDA = DURACION_1 / time; 
                  digitalWrite(TRIG_2, HIGH); 
                  delay(1);
                  digitalWrite(TRIG_2, LOW); 
                  DURACION_2 = pulseIn(ECO_2, HIGH);
                  DIST_FRENTE = DURACION_2 / time;
                  digitalWrite(TRIG_3, HIGH);     
                  delay(1);        
                  digitalWrite(TRIG_3, LOW);
                  DURACION_3 = pulseIn(ECO_3, HIGH);     
                  DIST_DERECHA = DURACION_3 / time;
              if(DIST_FRENTE < 80 && DIST_FRENTE > 0){ //GIRO
                VELOCIDAD = 50; PWM = map(VELOCIDAD, 0, 100, 0, 250); analogWrite(ENB, PWM);
                GIRO.write(L_DERECHA); delay(500);
                VELOCIDAD = 50; PWM = map(VELOCIDAD, 0, 100, 0, 250); analogWrite(ENB, PWM);
                delay(1300);
                GIRO.write(L_IZQUIERDA); delay(100); GIRO.write(L_CENTRO_D); delay(100); ACTIVO = 2;
                VELOCIDAD = 80; PWM = map(VELOCIDAD, 0, 100, 0, 250); analogWrite(ENB, PWM);
              }
          }
        //PARED 2
          if(PARED == 2){
            //VARIABLES
              SM = (DIST_DERECHA);
              SD = (20);
            //PID
              ET = SD - SM; //ERROR PROPORCIONAL 
              dE = (ET - Ep)/t; //ERROR DIFERENCIAL
              Ep = ET;
              iE = Eip + (t*ET); //ERROR INTEGRAL
              Eip = Ei;
              t = t + (0.053 + (PID/100)); //TIEMPO 
              PID = (KP*ET)+(KI*iE)+(KD*dE); //PID
              if(DIST_DERECHA < 40 || DIST_DERECHA < 0){
                GIRO.write(L_IZQUIERDA);
                delay(PID*10);
              }
                //ULTRASONICO
                  digitalWrite(TRIG_1, HIGH); 
                  delay(1);
                  digitalWrite(TRIG_1, LOW);
                  DURACION_1 = pulseIn(ECO_1, HIGH);
                  DIST_IZQUIERDA = DURACION_1 / time; 
                  digitalWrite(TRIG_2, HIGH); 
                  delay(1);
                  digitalWrite(TRIG_2, LOW); 
                  DURACION_2 = pulseIn(ECO_2, HIGH);
                  DIST_FRENTE = DURACION_2 / time;
                  digitalWrite(TRIG_3, HIGH);     
                  delay(1);        
                  digitalWrite(TRIG_3, LOW);
                  DURACION_3 = pulseIn(ECO_3, HIGH);     
                  DIST_DERECHA = DURACION_3 / time;
              if(DIST_IZQUIERDA < 40  || DIST_IZQUIERDA < 0){
                GIRO.write(L_DERECHA);
                delay(PID*5);
              }
            //VARIABLES
              SM_2 = (ANGULO);
              SD_2 = (90*ZONA);
            //PID
              //GIROSCOPIO
                if(INICIAL == 0){
                  mpu.update();  
                  if((millis()-timer)>100){
                    INICIAL = (mpu.getAngleZ());
                    timer = millis(); 
                  }
                }
                mpu.update();  
                if((millis()-timer)>10){  
                  CONTINUO = (mpu.getAngleZ());
                  timer = millis(); 
                  delay(50);
                  ANGULO = (CONTINUO - INICIAL);
                  if(PARED == 2){ //IZQUIERDA
                    ANGULO = ANGULO;
                  } 
                  if(PARED == 1){ //DERECHA
                    ANGULO = (-1*(ANGULO));
                  }                                       
                  if(ANGULO <= 90 && ANGULO >=1){
                    ZONA = 1;
                  }

                  if(ANGULO <= 180 && ANGULO >= 91){
                    ZONA = 2;
                  }

                  if(ANGULO <= 270 && ANGULO >= 181){
                    ZONA = 3;
                  }

                  if(ANGULO <= 360 && ANGULO >= 271){
                    ZONA = 4;
                  }
                  if(ANGULO <= 450 && ANGULO >=361){
                    ZONA = 5;
                  }

                  if(ANGULO <= 540 && ANGULO >= 451){
                    ZONA = 6;
                  }

                  if(ANGULO <= 630 && ANGULO >= 541){
                    ZONA = 7;
                  }

                  if(ANGULO <= 720 && ANGULO >= 631){
                    ZONA = 8;
                    VUELTA = 2;
                  }
                  if(ANGULO <= 810 && ANGULO >= 721){
                    ZONA = 9;
                  }

                  if(ANGULO <= 900 && ANGULO >= 811){
                    ZONA = 10;
                  }

                  if(ANGULO <= 990 && ANGULO >= 901){
                    ZONA = 11;
                  }
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

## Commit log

2024-08-17 Planos mecanismos
    Adjunto los planos detallados de todos las piezas usadas en el vehiculo
2024-08-17 CIrcuito modificado
    Subo la modificación del circuito con 3 fuentes
    [CIRCUITO_1.fzz]
2024-08-17 Segundo codigo
    Codigo de sensado con pruebas de movimiento
2024-08-29 Complementos
    Envio el archivo para impresión en resina, que se ocupo como remplazo
2024-08-29 Update README.md
    Explicación actualizada de inicio
2024-08-29 FOTOS
    Anexo fotos para el documento
2024-08-29 Update README.md
    Se acabo el commit
